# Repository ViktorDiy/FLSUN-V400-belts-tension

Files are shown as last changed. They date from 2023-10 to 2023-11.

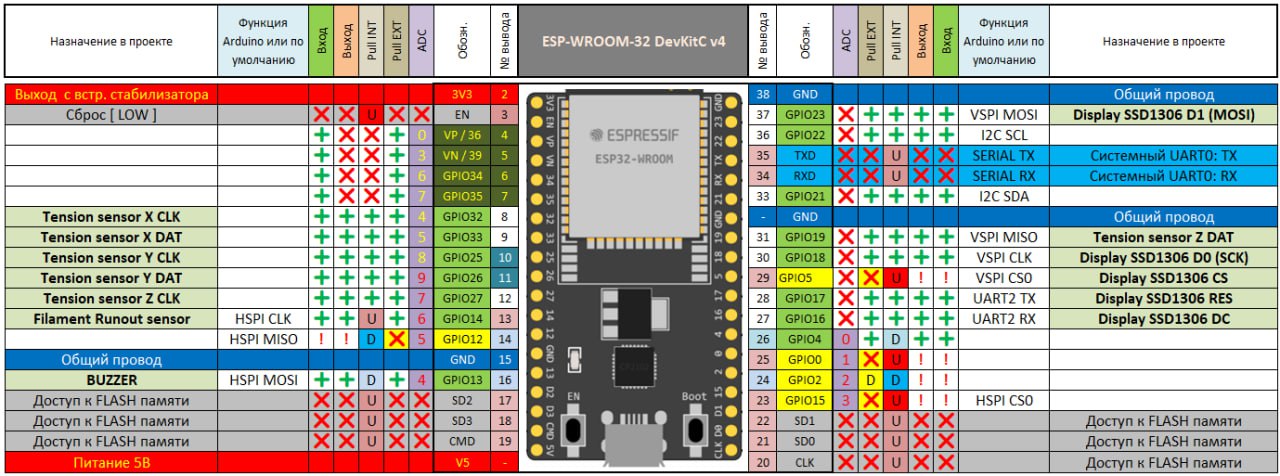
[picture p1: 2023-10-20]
ESP32 pinout.jpg

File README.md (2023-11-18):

Greetings to all owners of the wonderful FLSUN V400 3D printer!

I would like to share with you my development for measuring the tension of FLSUN V400 3D printer belts and monitoring it using a smart home system, including informing you about the achievement of critical tension values. 

My printer works 24/7, so it is critical for me to constantly monitor the tension of the belts. According to my observations, improper tension of the belts for 3d printers with delta kinematics significantly affects the print quality and can be harmful. 

Insufficient tension is bad because it increases the echo effect, and also, in general, reduces the quality of printing. 
It has also been observed that insufficient belt tension can significantly reduce the quality of the BED MASH. 
Excessive tension leads to rapid wear of the belts, increasing the load on the motors and bearings, which will result in faster wear and breakage. 
A very large and abrupt decrease in tension (for example, if the belt crash) leads to a strong change in the Z0 offset, which (some printer owners have observed) can lead to the breakage of the printer head, especially if it is very close to the table at that moment. It can also lead to deterioration of the surface of the PEI plate coating. 

All the methods of tension measurement known by me at the moment did not satisfy my requests, because, they looks strange from the point of view of metrology. And it is also impossible to implement monitoring, alerting, and integration with a smart home on their basis. 

After my analysis and a number of experiments with tension sensors, up to and including their integration into belt tensioners, I settled on the next most acceptable option from my point of view. 
A ready-made tension sensor from hands scales is used as a tension sensor, which can be easily placed in the printer rack. The donor of this sensor is the cheapest and most common canter scales, which can be easily bought on Aliexpress or Amazon or in local stores in your country. You can find a link to it in the general list of parts that I used in the project. 

Of course, using your imagination, you can use any other details and software that are available and convenient for you. I warn you right away that it is unlikely that you will be able to use the electronic part of the canter scales and the display for constant measurement of tension using my method, because the principle of measuring a canter scales is that first the value on the sensor is measured at zero weight, and then the value of the sensor is measured at the weight that you are measuring (if its value remains unchanged). These electronic canter scales cannot constantly measure weight/tension. 

The second main element of my project is the ESP32 development board, which is integrated with the Home Assistant smart home via ESPHome. Of course, you can develop software and hardware on ESP8266, Arduino, PlatformIO (developed in Ukraine), etc. 

ESP32 CP2102 Type-C 38 pin development board:
https://www.aliexpress.com/item/1005001636295529.html

The very common hx711 board is used as an amplifier/converter of tension measurement:
https://www.aliexpress.com/item/4000089335888.html
https://esphome.io/components/sensor/hx711
For each axis of the 3d printer we need a separate sensor and signal converter.
You should calibrate all 3 tension sensors separately and put calibration volumes in to ESPHome configuration file.

In my project I used 0.96 inch OLED IIC Serial White Display Module 128X64 I2C SSD1306 7 pin:
https://www.aliexpress.com/item/1005005563780197.html

Tension sensor donor - strain-gauge sensor from canter scales:
https://www.aliexpress.com/item/1005005627474221.html

For Second Edition you can use this sensor:
https://www.aliexpress.com/item/1005003692319461.html

X*3 furniture coupler intersection screw M4 thread and 30mm long:
https://www.aliexpress.com/item/1005004446281911.html
https://epicentrk.ua/ua/shop/bolt-styazhnoy-dekorativnyy-mezhsektsionnyy-m4-10-sht-khrom.html

X*3 brass nuts M4 and 8mm long for Second Edition Roller Fix:
https://www.aliexpress.com/item/1005006166300597.html

Very usefull Andreas Spiess video - https://youtu.be/iywsJB-T-mU?si=le56kaODWxQH_tsv

Some videos about this system, you can find here - https://www.facebook.com/profile.php?id=100094217897627

The finished device looks like this:





You should print project details is these positions:



Example of ESP32 pinout:



Sensor assembly:




Very lazy way for board installation:



You can reuse factory tension bolt. Put some spacer (for example x4 M4 nuts) for his length betterment.



You can reuse factory roller, but I prefer to use standard from Ali:



I use separate small 5V power adapter for HX711 + ESP32 power supply (connected to 220V in printer) but you can use DC-DC step down converter (24V->5V) or may be take 5V from V400 MCU.



Sensor pinout... For all my 10 scales Red wire = E+, Black = E-, colors for signal wires can be different, if during calibration you load more weight but get less volume - just swap these two wires. Sometimes they are mixed up at the factory in China.


Sensor calibration pocess:



Second Edition version. More easy to make, cheaper, 100% right geometry (you don't need to fix "china" geometry of donor details).

New sensor:

V400-0

Position for printing:

Orca screen

First and second versions compare:

V400-1

V400-2

V400-3



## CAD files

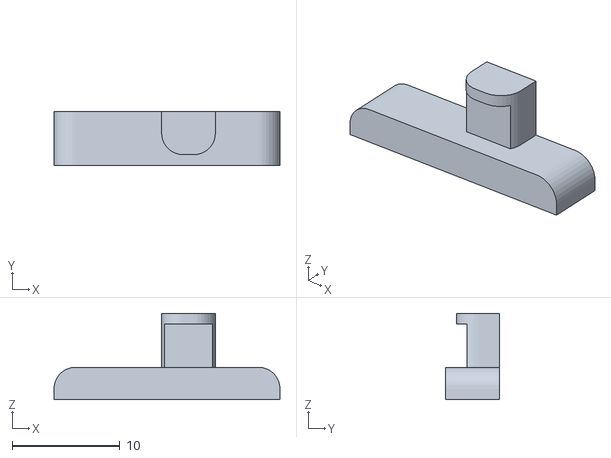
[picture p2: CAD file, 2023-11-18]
Cord fix Second Edition.STL
21.0 x 5.00 x 8.00

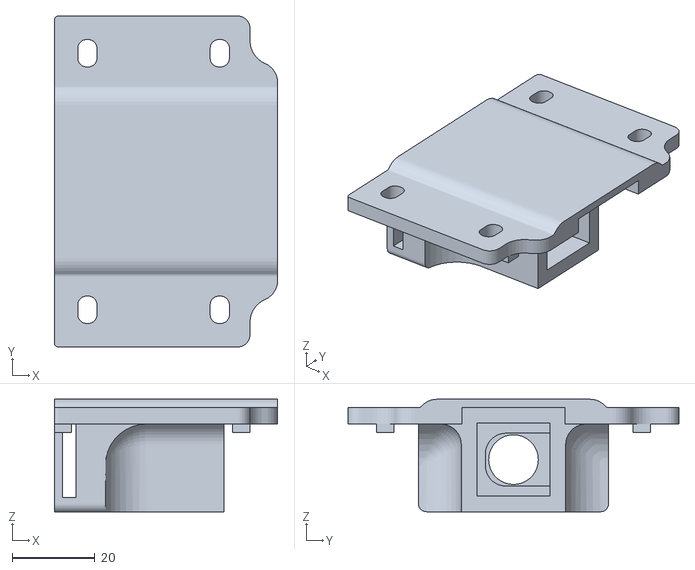
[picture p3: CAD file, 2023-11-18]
Tension platform Second Edition.STL
54.0 x 80.0 x 27.2

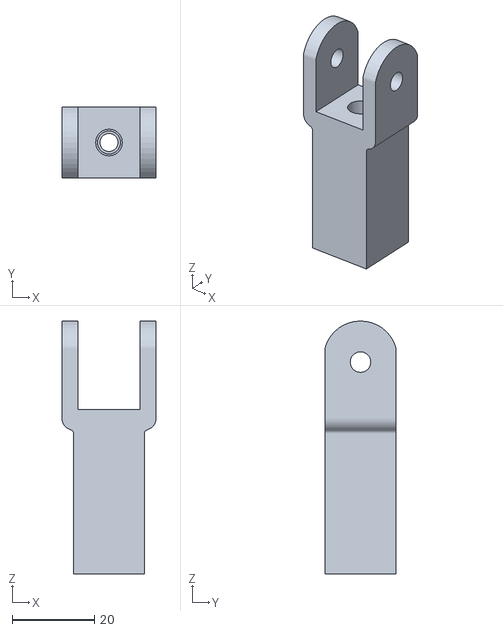
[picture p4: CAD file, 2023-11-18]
Roller fix Second Edition.STL
23.0 x 17.2 x 61.6

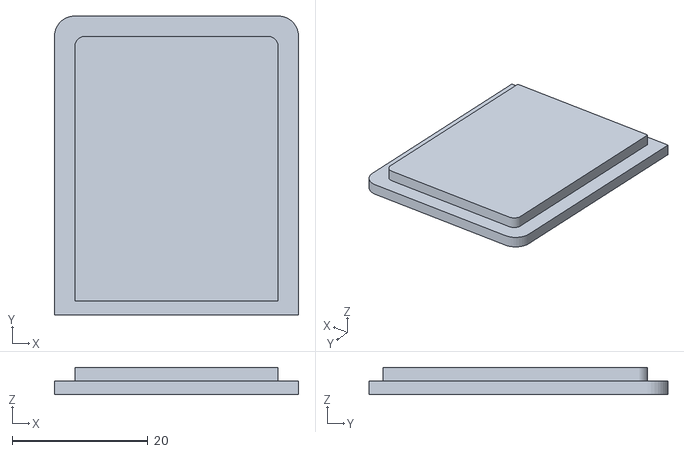
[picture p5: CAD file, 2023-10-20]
Display box cover.STL
36.0 x 44.1 x 4.00

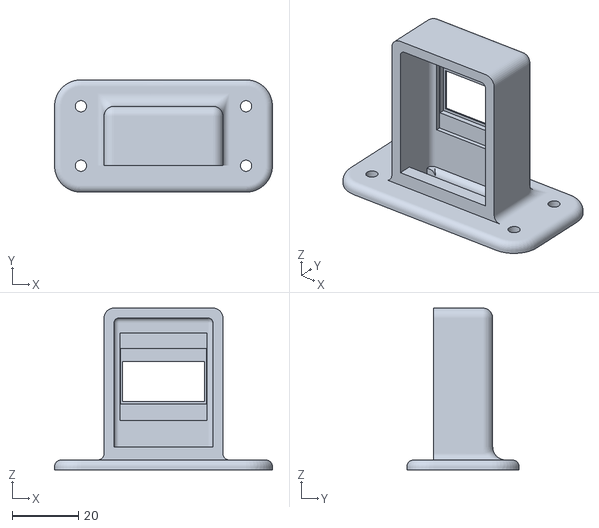
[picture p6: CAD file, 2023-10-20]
Display box.STL
66.0 x 34.0 x 49.0

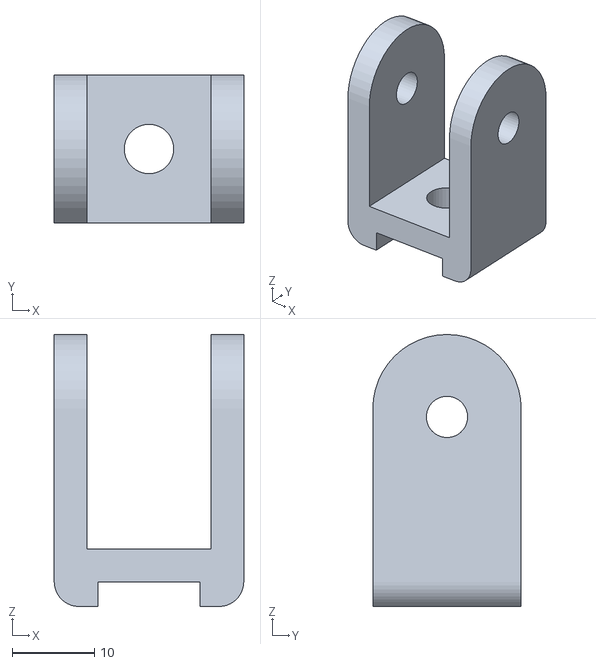
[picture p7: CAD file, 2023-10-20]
Roller fix.STL
23.0 x 18.0 x 33.0

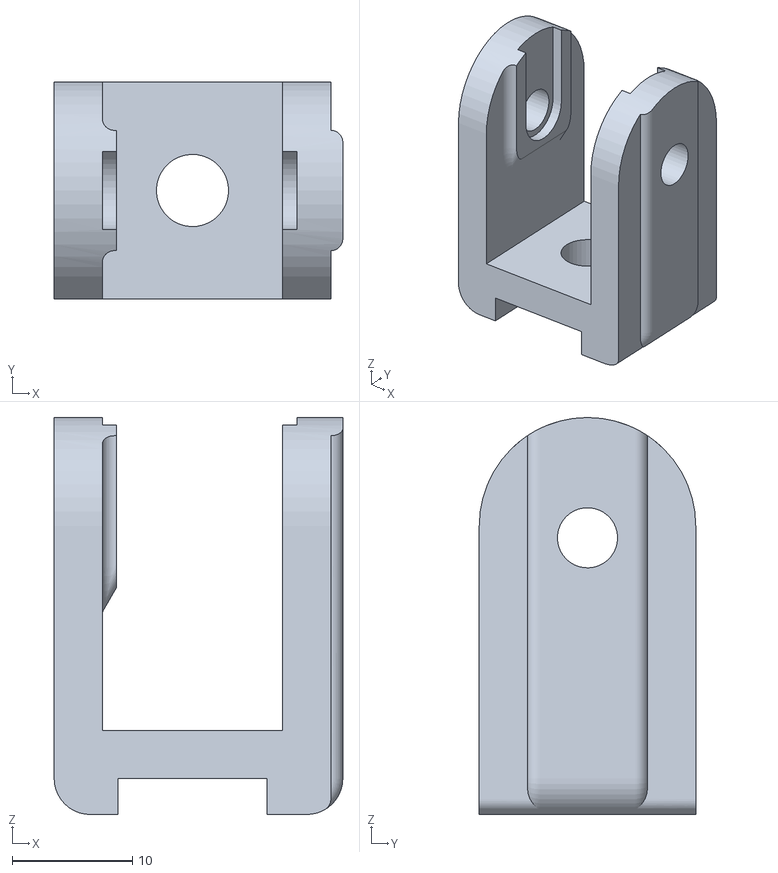
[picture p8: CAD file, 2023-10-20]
Roller fix reuse.STL
24.0 x 18.0 x 33.0

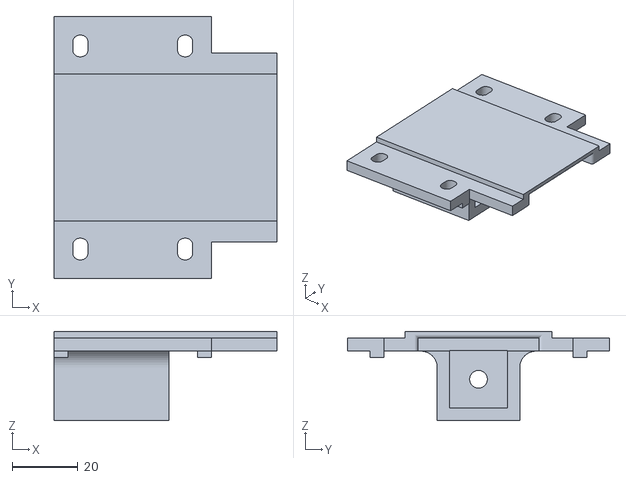
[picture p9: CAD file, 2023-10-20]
Tension platform.STL
68.0 x 80.0 x 27.2

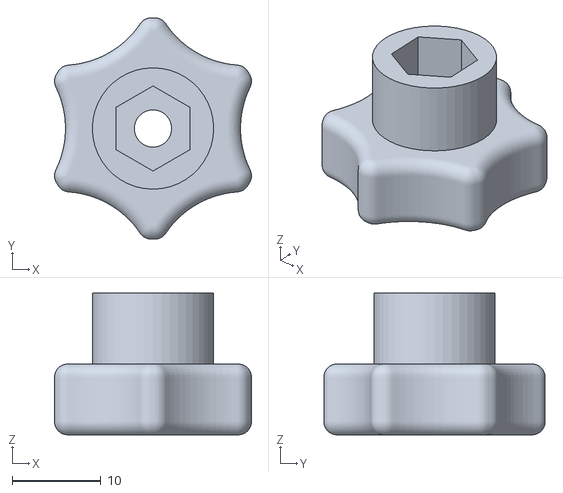
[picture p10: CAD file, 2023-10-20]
Tension bolt head.STL
22.2 x 25.0 x 16.0

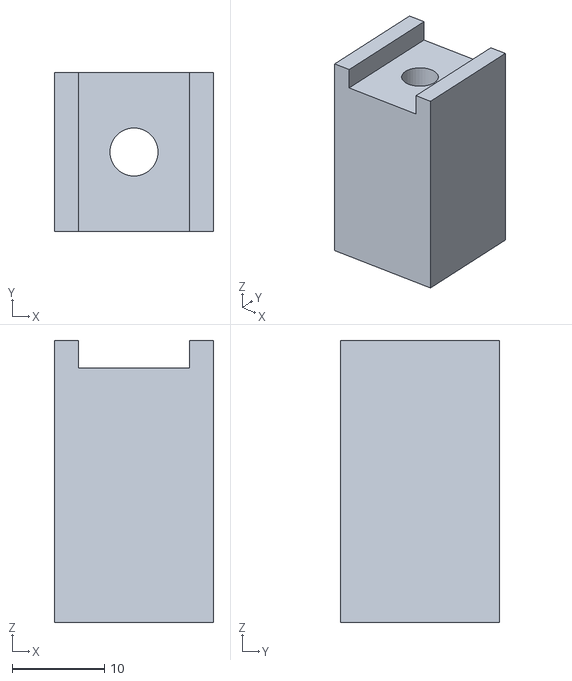
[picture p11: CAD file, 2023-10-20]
Tension bolt cover.STL
17.2 x 17.2 x 30.5

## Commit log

2023-11-18 Add files via upload
    Tension base with roller fix for second edition of system added
    [Cord fix Second Edition.STL, Roller fix Second Edition.STL, Tension platform Second Edition.STL]
2023-11-18 Update README.md for Second Edition of tension control system
